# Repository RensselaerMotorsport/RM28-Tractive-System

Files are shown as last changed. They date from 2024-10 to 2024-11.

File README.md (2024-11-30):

# RM28-TRACTIVE-SYSTEM

This respository currently contains several projects for Rensselaer Motorsport's RM28 FSAE competition car, along with some documentation, and spreadsheets for BOMs and calcs
* WIP RM28 Project - This project is the most up-to-date version of the 2024-2025 competition car's High Voltage System.

To open and work with these files, use the following software:
* LTSpice - Circuit simulation software used for preliminary mockups of circuit designs. The .asc files can be opened in other spice programs like ngspice or pspice, but these circuits were originally drafted in LTSpice
* KiCad - PCB design software used for creating schematics for manufacturing. These are either stored in .kicad_pcb files, or are gerber files packed away in zip archives
* Excel - For viewing of BSPD trip curve calculation sheet

Typical Circuits:
* Brake System Plausability Device (BSPD) - The custom circuit for RM28's safety circuit, designed to connect to our shutdown circuit. This is a fully analog safety circuit that activate the shutdown circuit when unsafe conditions (competition rules) are met.
    * The sensor values used for this circuit include the current sensor through the motor, and the voltage sensor from the accelerator pedal
    * See BSPD Current Sensor Trip Calculator.xlsx inside ./BSPD/ for calculations to determine the threshold voltage to activate this section of the circuit
* Ready to Move Light (RTML)
   * Blinking red LED if voltage outside accumulator is >60V, and if GLV on 
   * Static green LED if voltage outside accumulator is <60V, and if GLV on
* Voltage Indicator - Turns on LED indicator if voltage outside the accumulator container is greater than 60V. Must work in absence of GLV.
* ESF - Shows overall design of racecar electrical system. Includes datasheets, circuit diagrams, electrical architecture, and part numbers.

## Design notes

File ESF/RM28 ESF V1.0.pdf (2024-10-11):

Status BLANK
BLANK
OK
1 | | OK
1 | | OK
750 Ohms

### 50 W

750 W
1170 | V | OK
| mF | BLANK
| | OK
| sec
| V
95 | % | OK
212.268 W

### 0.53 A 0.00 sec

#DIV/0! | J

#DIV/0! | W

| | BLANK
#N/A | V | #N/A

#N/A | A | #N/A

Discharge

Bus Capacitance

Voltage

power @15 sec

Precharge

# series

# parallel

Ohmite 850F750E

Resistance

Resistor

Relay

Precharge Res Energy to 90% Average Power

Peak current
time to 90%

Ratio

Cont power

time

End of precharge

Resistance
Cont power

Discharge time (to 60V)

Peak power
Peak current

power @15 sec

Additional Comments

ending ratio

Relay voltage rating
Peak power | Relay current rating

delta V

Relay current rating

Relay voltage rating

Rules References

Normal State

EV.5.6; EV.7.2.2c

#Public

BLANK
OK
1 | | OK
1 | | OK
750 | Ohms | | #N/A
50 | W | | #N/A
750 | W | OK | #N/A
1170 | V | OK
212.268 W

### 0.53 A

0 | s | OK
| | BLANK
#N/A | V | #N/A

#N/A | A | #N/A

#N/A | | #N/A

Discharge

Voltage

TSMP
Resistor

Resistance
Cont power

# parallel

# series

Resistor Ohmite 850F750E
# parallel

# series

Resistance
Cont power

Peak power
Peak current

power @15 sec
Voltage

Relay

Normal State

BLANK
BLANK
BLANK
BLANK
Ohms | #N/A
W | #N/A
V | #N/A

Rules References
EV.5.8.4

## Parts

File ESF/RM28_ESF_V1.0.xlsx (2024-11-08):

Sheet: Overview
Instructions |  |  | Status
Input Cells: Cells that require user input have an orange background. Status Indicators: Cells, sections, and worksheets each have an overall status, indicated by blue background cells. Images and Schematics: For sections requiring images or schematics, paste the image over the specified area. Use high-resolution images to allow for zooming if needed, and then resize the image appropriately. Datasheets: Provide a hyperlink to the manufacturer's datasheet where requested. Additional Comments: Sections labeled "Additional Comments" are provided for documenting anything the team feels is not adequately covered in the specified fields. Completing these sections is optional. |  |  | Datasheets | OK
 |  |  | TS Schematics | OK
 |  |  | Accumulator | WARNING
 |  |  | Precharge/Discharge | OK
 |  |  | Charging | OK
 |  |  | Shutdown Circuit | OK
 |  |  | Torque Security | OK
 |  |  | Other | OK
 |  |  | Team Name | Rensselaer Motorsport
 |  |  | University | Rensselaer Polytechnic Institute
 |  |  | Competition Year | 2025
 |  |  | Max TS Voltage | 399 | V
 |  |  | Accumulator Fuse | 200 | A
Additional Comments
Template Revision History
Version | Date | Comment
2.4 | 2024-09-30 | Updated for 2025 rules and terminology, general bug fixes.
2.3 | 2023-10-29 | Updated for 2024 season.
2.2 | 2022-11-03 | Updated for 2023 season.
2.1 | 2021-10-22 | Updated for 2022 season.
2.0 | 2020-11-27 | Multiple updates and bug fixes.

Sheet: Datasheets
Status | OK
Battery Cell |  |  |  | OK
Make |  | Molicel
Model |  | P28A
Nominal Capacity |  | 2.8 | Ahr
Maximum Voltage |  | 4.2 | V
Nominal Voltage |  | 3.6 | V
Minimum Voltage |  | 2.5 | V
Max output current |  | 35 | A
Max continuous current |  | 25 | A
Max Cell temp |  | 60 | C
Cell Chemistry |  | LiNiMnCoO2 (NMC)
Datasheet |  | https://www.molicel.com/wp-content/uploads/INR18650P28A-V1-80093.pdf
SDS |  | https://www.molicel.com/wp-content/uploads/00058ar-Molicel-SDS-Y2020.pdf
Additional Comments
Conductors |  |  |  |  |  |  |  |  | OK
Manufacturer | Part Number | Size [mm2] | Voltage [V] | Ampacity [A] | Max Temp [C] | Datasheet |  | Location Used |  | Additional Comments |  |  |  |  | Rules References
Exrad | EXRAD–EF/EF-KW-50 | 50 | 1000 | 275 | 140 | High current TS wire (https://www.champcable.com/wp-content/uploads/2020/08/220.-EXRAD-ERGOFLEX-ERGOFLEX-Shielded-Thick-Wall-Battery-Cable-R1.pdf) |  | Accumulator to motor (through energy meter and MSD on respective - and + lines) & interior of accumulator | OK |  |  |  |  |  | EV.5.2.1 EV.5.2.5 EV.6.3 EV.6.3.2 EV.6.6.4
AWC | M22759/22-22 (https://www.awcwire.com/product/m22759_22-22) | 0.34 | 600 | 0.92 | 200 | Low current TS wire (https://www.awcwire.com/product/m22759_22-22) |  | IMD, Precharge, Discharge | OK | HV to IMD and pre/discharge wiring
Team Manufactured | Series Bus Bars | 68.54825 | N/A | 200 | N/A | 1100-H14 aluminum (https://www.mcmaster.com/88685K95/) |  | Series Cell Connections, HV component connections | OK | See Series bus bar calculations to the right
Team Manufactured | Maintenance plug Vertical offset cylinder | 121.7350884 | N/A | 200 | N/A | 6061 Aluminum Rod (https://www.mcmaster.com/2655N21/) |  | Maintenance plug Vertical offset cylinder | OK
Team Manufactured | Component HV bus bars | 68.54825 | N/A | 200 | N/A | 1100-H14 aluminum (https://www.mcmaster.com/88685K95/) |  | HV between component connections | OK | See variable length bus bar calculations to the right, examples of use include between IRs and accumulator HV connector
Fuses |  |  |  |  |  |  |  |  | OK
Manufacturer | Part Number | Voltage [V] | AC/DC | Current [A] | Interrupt [A] | Datasheet |  | Location Used |  | Additional Comments |  |  |  |  | Rules References
Heraeus | AL-H11 | N/A | DC | 35 | 10000 | AL-H11 (https://datasheet.datasheetarchive.com/originals/crawler/heraeus.com/31fe58e96e1a05e1dcb559314f291a55.pdf) |  | Cell-level fuseable links on purchased modules | OK |  |  |  |  |  | EV.5.2.1 EV.6.6
Bel Fuse | 0ZCK0020FF2G (https://www.mouser.com/ProductDetail/Bel-Fuse/0ZCK0020FF2G?qs=SRYZG9HaIQ1YaXTwF3oUbw%3D%3D) | 24 | DC | 0.25 | 100 | Bel Fuse 0ZCK (https://www.belfuse.com/resources/datasheets/circuitprotection/ds-cp-0zck-series.pdf) |  | Voltage sense lines on purchased cell modules | OK
Bel Fuse | 0AKNBK200-BB (https://www.mouser.com/ProductDetail/Bel-Fuse/0AKNBK200-BB?qs=vvQtp7zwQdNf0nJ%2FatZ4hA%3D%3D) | 500 | DC | 200 | 50000 | Bel Fuse (https://www.belfuse.com/resources/datasheets/circuitprotection/ds-CP-0AKN-series.pdf) |  | Accumulator main fuse | OK
Schurter Inc. | 8020.5071.G (https://www.mouser.com/ProductDetail/Schurter/8020.5071.G?qs=YfC6cSmZ4rqo%252BdI%252BgQjFCw%3D%3D) | 400 | DC | 2 | 1500 | IMD Fuse (https://www.schurter.com/en/datasheet/typ_SHF_6.3x32.pdf) |  | IMD supply lines | OK | HV to IMD (needed due to wires >= 150mm)
Bel Fuse | 0ADKC5000-BE (https://www.mouser.com/ProductDetail/Bel-Fuse/0ADKC5000-BE?qs=HXFqYaX1Q2xXpuf%2FgyvHFg%3D%3D) | 500 | DC | 5 | 20000 | Energy Meter Fuse (https://www.mouser.com/datasheet/2/643/ds_cp_0adkx_series-1960352.pdf) |  | Energy meter positive line | OK
Resistors |  |  |  |  |  |  |  |  |  |  |  | OK
Manufacturer | Part Number | Voltage [V] | Resistance [Ω] | Power [W] | Power for 15 sec [W] | Heatsink [°C/W] (Enter "None" if no heatsink) |  |  | Datasheet |  | Location Used |  | Additional Comments & Heatsink Part Number(s) |  |  |  | Rules References
Ohmite | 850F750E (https://www.mouser.com/ProductDetail/Ohmite/850F750E?qs=%2Fkw1Ka6y2YmeEqAmz%252BCsrw%3D%3D) | 1170 | 750 | 50 | 750 | 3 |  |  | 850F750E (https://www.ohmite.com/assets/images/res-89.pdf) |  | Precharge/Discharge | OK | Manufacturer tests at 5x rated power for 5sec. 250W>212W peak. 50W>46W avg. |  |  |  | EV.5.2.1 EV.5.6 EV.5.8.4
Caddock Electronics Inc. | MP925-10.0K-1% (https://www.mouser.com/ProductDetail/Caddock/MP925-10.0K-1?qs=YqNA2qefETA%2FE%2Fk%2F%252BKWLww%3D%3D) | 500 | 10000 | 25 | N/A | None |  |  | MP925 (https://www.mouser.com/datasheet/2/62/MP9000_Series-1052.pdf) |  | TSMP | OK
Contactors/Relays |  |  |  |  |  |  |  |  | OK
Manufacturer | Part Number | Voltage [V] | Continuous Current [A] | Max Interrupt Current [A] | Normal State | Datasheet |  | Location Used |  | Additional Comments |  |  |  |  | Rules References
Kilovac | LEV200A4NAA (https://www.mouser.com/ProductDetail/TE-Connectivity-Kilovac/LEV200A4NAA?qs=FoJTTr54RLTOub1ORrXpDA%3D%3D) | 900 | 500 | 1.1 | NO | LEV200A4NAA (https://www.mouser.com/datasheet/2/418/9/ENG_CS_5_1773450_5_sec7_LEV200_0313_5_1773450_5_Se-3350705.pdf) |  | IRs, Inside Accumulator Container | OK |  |  |  |  |  | EV.5.2.1 EV.5.4 EV.5.6
Cynergy3 | DBT71205F-HR (https://www.mouser.com/ProductDetail/Cynergy3/DBT71205F-HR?qs=OlC7AqGiEDknK2jB3AhN5A%3D%3D) | 3500 | 3 | 2 | NC | DBT71205F-HR (https://www.mouser.com/datasheet/2/657/cynergy3_d_hr_v2-1892317.pdf) |  | Discharge | OK
Cynergy3 | DAT71205F-HR (https://www.mouser.com/ProductDetail/Cynergy3/DAT71205F-HR?qs=OlC7AqGiEDlIL4KVHc3FLw%3D%3D) | 3500 | 3 | 2 | NO | DAT71205F-HR (https://www.mouser.com/datasheet/2/657/cynergy3_d_hr_v2-1892317.pdf) |  | Precharge | OK
Connectors |  |  |  |  |  |  |  | OK
Manufacturer | Part Number | Voltage [V] | Ampacity [A] | Wire Size [mm2] | Datasheet |  | Location Used |  | Additional Comments |  |  |  |  | Rules References
Amphenol | MSDM5002 (https://www.mouser.com/ProductDetail/Amphenol-PCD-Shenzhen/MSDM5002?qs=LcEtihlZWqbc1RsOqxB6zA%3D%3D) | 1000 | 500 | 50 | MSD Plug (https://www.mouser.com/datasheet/2/18/1/msd_m_xxxx_rev_a_cdr-1853453.pdf) |  | MSD Plug | OK |  |  |  |  |  | EV.5.2.1 EV.5.9 EV.6.3.3
Amphenol | MSDF000R (https://www.mouser.com/ProductDetail/Amphenol-PCD-Shenzhen/MSDF000R?qs=LcEtihlZWqaGMLWux0l6Dw%3D%3D) | 1000 | 500 | 50 | MSD Receptacle (https://www.mouser.com/datasheet/2/18/Amphenol_08092019_MSDF000R-1626989.pdf) |  | MSD Receptacle | OK
Amphenol | PL082Y-301-10M6-2 (https://www.mouser.com/ProductDetail/Amphenol-Technical-Products/PL082Y-301-10M6-2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) | 1000 | 300 | 50 | PL082Y-301-10M6-2 (https://www.mouser.com/datasheet/2/18/1/Amphneol_01182021_PowerLok_G2_Product_Catalog_2020-1955456.pdf) |  | HV Out Receptacle | OK
Amphenol | PL282Y-301-50 (https://www.mouser.com/ProductDetail/Amphenol-Technical-Products/PL282Y-301-50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) | 1000 | 300 | 50 | PL282Y-301-50 (https://www.mouser.com/datasheet/2/18/1/c_powerlok_right_angle_plugs_1_2_3_way_cdr-1701769.pdf) |  | HV Out Plug | OK
Team Manufactured | Maintenance Plug Bus Bar | N/A | 200 | 68.54825 | 1100-H14 aluminum (https://www.mcmaster.com/88685K95/) |  | Maintenance Plugs | OK | See calculations to the right
Littelfuse | 03450613H | 600 | 20 | N/A | Energy meter fuse holder (https://www.molex.com/en-us/products/part-detail/192210241?display=pdf) |  | Energy meter fuse holder | OK | Soldered terminals, low current fuse
Amphenol | HVSL633063A106I | 800 | 40 | 16 | AC In (https://mgchemicals.com/downloads/tds/tds-4223f-l.pdf) |  | Charger input | OK | AC in to charger
Pomona Electronics | 72930 | 1000 | 36 | N/A | TSMP (https://www.awcwire.com/product/m22759_22-22) |  | TSMP - start panel | OK | TSMP connector. One red, one black, same part electrically
Molex | 192210241 | N/A | 230 | 55 | TS Ring Terminals (https://www.mouser.com/ProductDetail/Bel-Fuse/0ADKC5000-BE?qs=HXFqYaX1Q2xXpuf%2FgyvHFg%3D%3D) |  | Energy meter, Motor, MSD, Main fuse, IRs | OK | Ring terminals crimped onto main TS cable. Used in various locations when attaching to bolted connection (HVD, energy meter, motor phases, main fuse, AIRs)
Insulating Materials |  |  |  |  |  |  |  |  |  | OK
Manufacturer | Part Number | Thickness [mm] | Dielectric strength [V/mm] | Voltage Rating [V] | Max Temp [C] | Flammability Rating | Datasheet |  | Location Used |  | Additional Comments |  |  |  |  | Rules References
McMaster-Carr | 85345K651 | 62.5 | 350 | 21875 | 137.778 | UL 94 V-0 | Accumulator plate hard insulation (https://www.mcmaster.com/85345K651/) |  | Accumulator | OK | Used on the underside of the horizontal plate that divides segments from components |  |  |  |  | EV.5.2.1 EV.5.2.2.a EV.5.2.3 EV.5.4.4 EV.6.2 EV.6.5.5.a
MYJOR | Kapton Tape | 1 | 4500 | 4500 | 350 | N/A | Kapton tape (https://www.amazon.com/Temperature-Kapton-Professional-Protecting-Circuit/dp/B08NY4914D) |  | Segments, accumulator container edges, motor connections | OK
CIE Solutions | Gen 2 Lithium Block Module | 3.4 | 26000 | 88400 | 105 | UL 94 V-0 | Cell modules (https://www.cie-solutions.com/lithium-block-gen2) |  | Modules | OK | Purchased modules made of Glass-Filled Fire Retardent ABS
3M | FP-301 | 0.76 | 789.4736842 | 600 | 125 | N/A | Bus bar heat shrink (https://multimedia.3m.com/mws/media/23031O/3m-heat-shrink-tubing-fp-301-data-sheet.pdf) |  | Bus Bars | OK
3DX Tech | PCA03FR200750BK00 | 5 | 26000 | 130000 | 137 | UL 94 V-0 | 3D printing filament (https://cdn.shopify.com/s/files/1/0625/4185/6821/files/FIREWIRE_FR_PCABS_TDS_v3.pdf?v=1723942765) |  | Maintainence Plug Handle | OK
Dupont | 93554 | 0.13 | 28150 | 3659.5 | 220 | UL 94 V-0 | Nomex (https://materials-direct.com/product/dupont-nomex-410-0-13mm/) |  | Segement dividing walls, accumulator container inside walls | OK
MG Chemicals | 4223F-55ML | 2 | 1000 | 2000 | 125 | N/A | Conformal Coat (https://mgchemicals.com/downloads/tds/tds-4223f-l.pdf) |  | Team manufactured PCBs (RTM, Voltage Indicator, etc.) | OK | UV-A flourescent
Anti Seize Technology | 17214 | 0.0508 | 66929 | 3399.9932 | 121 | N/A | Insulative Spray Coating (https://www.grainger.com/product/ANTI-SEIZE-TECHNOLOGY-Insulating-Varnish-Red-34D505) |  | Container walls, segment mounting brackets | OK

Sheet: TS Schematics
Status | OK
Tractive System Schematic |  |  |  |  | Accumulator TS Schematic |  |  |  | Additional Comments
 |  |  |  |  |  |  |  |  | Voltage Indicator Schematic:
Vehicle Tractive System Schematic Shows |  |  |  | OK | Accumulator TS Schematic Shows |  |  | OK
Rules References |  |  |  |  | Rules References
 |  | Shows details of all TS circuits outside of accumulator | TRUE | OK |  | Details of all TS circuits within accumulator | TRUE | OK
 |  | Accumulator is shown as a single element (without internal details) | TRUE | OK |  | All wire gauges labeled | TRUE | OK
 |  | All wire gauges labeled | TRUE | OK |  | All fuses labeled with ampacity | TRUE | OK
 |  | All fuses labeled with ampacity | TRUE | OK | EV.6.6.6 | All wires > 150mm have a fuse within the first 150mm from the source | TRUE | OK
EV.6.6.6 |  | All wires > 150mm have a fuse within the first 150mm from the source | TRUE | OK |  | Fuse locations represent physical location | TRUE | OK
 |  | Fuse locations represent physical location | TRUE | OK |  | Connectors labeled with Make/Model | TRUE | OK
 |  | Enclosures shown | TRUE | OK |  | Standard schematic symbols used | TRUE | OK
 |  | Connectors labeled with Make/Model | TRUE | OK |  | All text is readable (zooming is allowed) | TRUE | OK
 |  | Standard schematic symbols used | TRUE | OK | EV.5.4 | IRs | TRUE | OK
 |  | All text is readable (zooming is allowed) | TRUE | OK | EV.5.3 | Maintenance plugs | TRUE | OK
EV.5.8 |  | TSMPs | TRUE | OK |  | Cells (details of all intercell connections may be abstracted) | TRUE | OK
 |  | Motor Controller | TRUE | OK | EV.5.7 | Accumulator Indicator (must be powered directly by TS) | TRUE | OK
 |  | Motor | TRUE | OK
EV.5.8.5 |  | TSMPs not fused | TRUE | OK
Must be shown on at least one schematic |  |  |  | OK
Rules References
EV.7.6 |  | IMD | TRUE | OK
EV.5.5 |  | MSD | TRUE | OK
EV.5.6 |  | Precharge | TRUE | OK
EV.5.6 |  | Discharge | TRUE | OK
EV.3.2; EV.5.1.3 |  | Energy Meter (shunt and TS sense connection) | TRUE | OK
EV.5.6.3.b |  | Discharge still functions when MSD is opened | TRUE | OK
EV.5.6.3.c |  | Discharge is not fused | TRUE | OK

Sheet: Accumulator
Status | WARNING
Segment-to-Segment Connection |  |  |  | Series |  | OK
Maximum TS Voltage |  |  |  | 399 | V | OK
Nominal TS Voltage |  |  |  | 342 | V
Total Cells |  |  |  | 570
Segment Data |  |  |  |  |  |  |  |  | OK | BMS |  |  |  |  | WARNING | Maintenance Plugs |  |  |  | OK | Insulating Materials |  |  |  |  | OK | Additional Comments
Cell Connection Order |  |  | Parallel then Series |  |  |  |  |  | OK | BMS Type |  |  | Centralized |  | OK | Connector |  | Team Manufactured Maintenance Plug Bus Bar |  | OK | Between cells and accum. container |  |  | Dupont 93554 |  | OK
Segment | Parallel cells | Series cells | Temp Sensors | Accumulator Number | Max Voltage [V] |  | Segment Energy [MJ] |  |  | BMS Source |  |  | Purchased |  | OK | Ampacity |  | 200 | A | OK | Voltage Rating |  |  | 3659.5 | V | OK
 |  |  |  |  |  |  |  |  |  | Make | Orion | Model | BMS2 180-Cell |  | OK | Segment Fuse |  |  |  |  | Temperature Rating |  |  | 220 | C | OK
1 | 6 | 19 | 95 | 1 | 79.8 |  | 4.826304 |  | OK | Galvanic Isolation TS to GLV |  |  | 1500 | V | OK | Segment Fuse Ampacity |  | #N/A | A |  | Flammability Rating |  |  | UL 94 V-0
2 | 6 | 19 | 95 | 1 | 79.8 |  | 4.826304 |  | OK | Galvanic Isolation between segments |  |  | 2500 | V | OK | IR |  |  |  |  | On top of cells |  |  | CIE Solutions Gen 2 Lithium Block Module |  | OK
3 | 6 | 19 | 95 | 1 | 79.8 |  | 4.826304 |  | OK | Galvanic Isolation device |  |  |  |  |  | Make/Model |  | Kilovac LEV200A4NAA |  | OK | Voltage Rating |  |  | 88400 | V | OK
4 | 6 | 19 | 95 | 1 | 79.8 |  | 4.826304 |  | OK | Gavlanic Isolation device datasheet |  |  |  |  |  | Contact Voltage Rating |  | 900 | V | OK | Temperature Rating |  |  | 105 | C | OK
5 | 6 | 19 | 95 | 1 | 79.8 |  | 4.826304 |  | OK | Voltage Sense Leads |  |  |  |  |  | Max switching current |  | 1.1 | A |  | Flammability Rating |  |  | UL 94 V-0
6 |  |  |  |  | 0 |  | 0 |  |  | Maximum Unfused Lead Length |  |  | 5 | mm | OK | Max continuous current |  | 500 | A | OK | Separating IRs and Fuse from cells |  |  | McMaster-Carr 85345K651 |  | OK
7 |  |  |  |  | 0 |  | 0 |  |  | Sense Lead Overcurrent Protection Device |  |  | Bel Fuse 0ZCK0020FF2G |  | OK | Main Fuse |  |  |  |  | Voltage Rating |  |  | 21875 | V | OK
8 |  |  |  |  | 0 |  | 0 |  |  | Overcurrent Location |  |  | BMS PCB |  | OK | Main Fuse |  | Bel Fuse 0AKNBK200-BB |  | OK | Temperature Rating |  |  | 137.778 | C | OK
9 |  |  |  |  | 0 |  | 0 |  |  | Overcurrent Other Location |  |  |  |  |  | Main fuse ampacity |  | 200 | A |  | Flammability Rating |  |  | UL 94 V-0
10 |  |  |  |  | 0 |  | 0 |  |  | Overcurrent Voltage Rating |  |  | 24 | V | WARNING | Main fuse voltage |  | 500 | V | OK
11 |  |  |  |  | 0 |  | 0 |  |  | Temperature Sensors |  |  |  |  |  | MSD
12 |  |  |  |  | 0 |  | 0 |  |  | Temp Sensor Location |  |  | On cell terminal |  | OK | MSD |  | Amphenol MSDM5002 |  | OK
13 |  |  |  |  | 0 |  | 0 |  |  | Distance to cell terminal |  |  |  | mm |  | Ampacity |  | 500 | A | OK
14 |  |  |  |  | 0 |  | 0 |  |  | Cells sensed per sensor |  |  | 1 | cells | OK
15 |  |  |  |  | 0 |  | 0 |  |  | Thermal Contact material used |  |  | 3M Scotch-Weld Epoxy Adhesive 2216
16 |  |  |  |  | 0 |  | 0 |  |  | Thermal contact material datasheet |  |  | https://multimedia.3m.com/mws/media/2366022O/3m-scotch-weld-epoxy-adhesive-2216-b-a-gray.pdf |  | OK
17 |  |  |  |  | 0 |  | 0 |  |  | Thermal contact material conductivity |  |  | 0.394 | W/(m∙K) | OK
18 |  |  |  |  | 0 |  | 0 |  |  | Thermal contact material thickness |  |  | 1 | mm | OK
 |  |  |  |  |  |  |  |  |  | Percent of cells sensed |  |  | 83.33333333 | % | OK
Picture of Maintenance Plugs |  |  |  |  |  |  |  |  | Picture of Cell Connections |  |  |  |  |  |  |  | Picture of Temperature Sensor Location |  |  |  |  |  |  | Picture of Fuse and IRs Separation from Cells |  |  |  |  |  | Picture of Segment Insulation between Cell Terminals and Sides of Accumulator Container |  |  | Picture of Insulation on Top of Segment
Maintenance Plug(s) Picture Shows |  |  |  |  |  |  | OK |  | Cell Connections Picture Shows |  |  |  |  |  | OK |  | Temperature Sensor Picture Shows |  |  |  |  |  | OK | Fuse and IRs Separation Picture Shows |  |  |  |  | OK | Segment Insulation Picture Shows |  | OK | Segment Insulation Picture Shows |  | OK
Unique Configuration of plugs |  |  |  |  |  | TRUE | OK |  | Bolted connections have positive locking |  |  |  |  | TRUE | OK |  | Temp sensor in direct contact with terminal or busbar |  |  |  |  | TRUE | OK | Fuse and IRs are separated from cells |  |  |  | TRUE | OK | Insulation between cells and accumulator container | TRUE | OK | Insulation on top of cells (air not acceptable) | TRUE | OK
Non-conductive on un-necessary surface |  |  |  |  |  | TRUE | OK |  | Location of parallel cell overcurrent for parallel cells |  |  |  |  | TRUE | OK |  | Distance from sensor to cell negative terminal connection |  |  |  |  | TRUE | OK | Additional Comments |  |  |  |  | Rules References | Additional Comments |  | Rules References | Additional Comments |  | Rules References
Accessible without any additional accumulator disassembly |  |  |  |  |  | TRUE | OK |  | BMS voltage sense fuse location |  |  |  |  | TRUE | OK |  | Additional Comments |  |  |  |  |  | Rules References | The fuse is the flat dark green box on the top left. The fuse and IRs are separated by a 4130 steel plate as well as Nomex paper which are both nonflamable. The insulation is where the two highlighted blue lines are in the image |  |  |  |  | EV.5.4.4 | Insulation is nomex paper which will be placed on walls, pictured in blue and teal. As well there will be insulation on the interior walls on the sides and back pictured in pink. Highlighted in light blue is where G10 insulation will be placed on the top of the segement enclosure |  | EV.5.2.2.a EV.5.2.3 | Insulation is Fire Retardant, Glass Filled ABS |  | EV.5.2.2.a EV.5.2.3
Positive Locking |  |  |  |  |  | TRUE | OK |  | Additional Comments |  |  |  |  |  | Rules References |  | Thermistor directly on negative cell terminal. No dimension needed |  |  |  |  |  | EV.7.5
Additional Comments |  |  |  |  |  |  | Rules References |  | Nylon patch bolts into OEM component, left is series connections, right is parallel (fused, wire bonded) connections |  |  |  |  |  | EV.6.4.1 EV.6.4.3 EV.7.4.4.a
Our maintainence plug solution uses a nylon patch bolt to hold down an elevated bus bar connected to the end module of the segment. The bolts have a 3d printed cap(in yellow) made of FR ABS that are bonded to the bolts to unscrew without tools. The elevated aluminum cylinder will have a cover over it similar to the bus bar covers to ensure it can not be accidentally touched. Bus bars will be removed using an ABS printed attachment. |  |  |  |  |  |  | EV.5.3
Parallel Cell Fusing |  |  |  |  | WARNING | Rules Referenes
Source |  |  | Purchased |  | OK | EV.6.6.3 EV.6.6.5
Make/Model |  |  | Heraeus AL-H11 |  | OK
Continuous Current |  |  | 35 | A | WARNING
Continuous Current |  |  |  | A
Test Data Summary
Tests at current 1 |  |  | 0 |  |  |  |  | #N/A
Tests at current 2 |  |  | 0 |  |  |  | #N/A | #N/A
Tests at current 3 |  |  | 0 |  |  |  | #N/A
Tests at current 4 |  |  | 0
See Fusible Link Testing Guideline on FSAEOnline.com
Testing | Current [A] | Time to blow [s]
Test 1
Test 2
Test 3
Test 4
Test 5
Test 6
Test 7
Test 8
Test 9
Test 10
Test 11
Test 12
Test 13
Test 14
Test 15
Test 16

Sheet: PrechargeDischarge
Status | OK
Precharge |  |  |  | OK | Discharge |  |  | OK | Vehicle TSMP |  |  | OK | Rules References
Resistor |  | Ohmite 850F750E |  | OK | Resistor | Ohmite 850F750E |  | OK | Resistor | Caddock Electronics Inc. MP925-10.0K-1% |  | OK | EV.5.8.4
# parallel |  | 1 |  | OK | # parallel | 1 |  | OK | # parallel | 1 |  | OK
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

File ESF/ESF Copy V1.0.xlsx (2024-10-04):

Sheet: Overview
Instructions |  |  | Status
-All cells for input have an orange background. -Cells, sections and worksheets have an overall status. The status cells have a blue background. -For sections which require an image or schematic, the image should be pasted and located over the specified area. Images should be pasted at a high resolution and then resized. This allows the reader to zoom into the image if more resolution is required. -Where datasheets are requested, a hyperlink to the datasheet from the manufacturer must be provided. -Additional Comments sections are provided throughout for documentation of things which the team feels are not adequately documented in the provided fields. These are optional and do not need to be completed. |  |  | Datasheets | BLANK
 |  |  | TS Schematics | BLANK
 |  |  | Accumulator | BLANK
 |  |  | Precharge/Discharge | BLANK
 |  |  | Charging | BLANK
 |  |  | Shutdown Circuit | BLANK
 |  |  | Torque Security | BLANK
 |  |  | Other | BLANK
 |  |  | Team Name | Rensselaer Motorsport
 |  |  | University | Rensselaer Polytechnic Insitute
 |  |  | Competition Year | 2024
 |  |  | Max TS Voltage | 399 | V
 |  |  | Accumulator Fuse | #N/A | A
Additional Comments
Template Revision History
Version | Date | Comment
2.3 | 2023-10-29 | Updated for 2024 season.
2.2 | 2022-11-03 | Updated for 2023 season.
2.1 | 2021-10-22 | Updated for 2022 season.
2.0 | 2020-11-27 | Multiple updates and bug fixes.

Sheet: Datasheets
Status | BLANK
Battery Cell |  |  |  | OK
Make |  | Molicel
Model |  | P28A
Nominal Capacity |  | 2.8 | Ahr
Maximum Voltage |  | 4.2 | V
Nominal Voltage |  | 3.6 | V
Minimum Voltage |  | 2.5 | V
Max output current |  | 35 | A
Max continuous current |  | 25 | A
Max Cell temp |  | 60 | C
Cell Chemistry |  | LiNiMnCoO2 (NMC)
Datasheet |  | https://www.molicel.com/wp-content/uploads/INR18650P28A-V1-80093.pdf
SDS |  | https://www.molicel.com/wp-content/uploads/00058ar-Molicel-SDS-Y2020.pdf
Additional Comments
Conductors |  |  |  |  |  |  |  |  | BLANK
Manufacturer | Part Number | Size [mm2] | Voltage [V] | Ampacity [A] | Max Temp [C] | Datasheet |  | Location Used |  | Additional Comments |  |  |  |  | Rules References
 |  |  |  |  |  |  |  |  | BLANK |  |  |  |  |  | EV.5.2.1 EV.5.2.5 EV.6.3 EV.6.3.2 EV.6.6.4
Fuses |  |  |  |  |  |  |  |  | BLANK
Manufacturer | Part Number | Voltage [V] | AC/DC | Current [A] | Interrupt [A] | Datasheet |  | Location Used |  | Additional Comments |  |  |  |  | Rules References
 |  |  |  |  |  |  |  |  | BLANK |  |  |  |  |  | EV.5.2.1 EV.6.6
Resistors |  |  |  |  |  |  |  |  |  |  |  | BLANK
Manufacturer | Part Number | Voltage [V] | Resistance [Ω] | Power [W] | Power for 15 sec [W] | Heatsink [°C/W] (Enter "None" if no heatsink) |  |  | Datasheet |  | Location Used |  | Additional Comments |  |  |  | Rules References
 |  |  |  |  |  |  |  |  |  |  |  | BLANK |  |  |  |  | EV.5.2.1 EV.5.6 EV.5.8.4
Contactors/Relays |  |  |  |  |  |  |  |  | BLANK
Manufacturer | Part Number | Voltage [V] | Continuous Current [A] | Max Interrupt Current [A] | Normal State | Datasheet |  | Location Used |  | Additional Comments |  |  |  |  | Rules References
 |  |  |  |  |  |  |  |  | BLANK |  |  |  |  |  | EV.5.2.1 EV.5.4 EV.5.6
Connectors |  |  |  |  |  |  |  | BLANK
Manufacturer | Part Number | Voltage [V] | Ampacity [A] | Wire Size [mm2] | Datasheet |  | Location Used |  | Additional Comments |  |  |  |  | Rules References
 |  |  |  |  |  |  |  | BLANK |  |  |  |  |  | EV.5.2.1 EV.5.10 EV.6.3.3
Insulating Materials |  |  |  |  |  |  |  |  |  | BLANK
Manufacturer | Part Number | Thickness [mm] | Dielectric strength [V/mm] | Voltage Rating [V] | Max Temp [C] | Flammability Rating | Datasheet |  | Location Used |  | Additional Comments |  |  |  |  | Rules References
 |  |  |  |  |  |  |  |  |  | BLANK |  |  |  |  |  | EV.5.2.1 EV.5.2.2.a EV.5.2.3 EV.5.4.4 EV.6.2 EV.6.5.5.a

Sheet: TS Schematics
Status | BLANK
Tractive System Schematic |  |  |  | Accumulator TS Schematic |  |  | Additional Comments
Vehicle Tractive System Schematic Shows |  |  | BLANK | Accumulator TS Schematic Shows |  | BLANK
Rules References |  |  |  | Rules References
 |  | Shows details of all TS circuits outside of accumulator | BLANK |  | Details of all TS circuits within accumulator | BLANK
 |  | Accumulator is shown as a single element (without internal details) | BLANK |  | All wire gauges labeled | BLANK
 |  | All wire gauges labeled | BLANK |  | All fuses labeled with ampacity | BLANK
 |  | All fuses labeled with ampacity | BLANK | EV.6.6.6 | All wires > 150mm have a fuse within the first 150mm from the source | BLANK
EV.6.6.6 |  | All wires > 150mm have a fuse within the first 150mm from the source | BLANK |  | Fuse locations represent physical location | BLANK
 |  | Fuse locations represent physical location | BLANK |  | Connectors labeled with Make/Model | BLANK
 |  | Enclosures shown | BLANK |  | Standard schematic symbols used | BLANK
 |  | Connectors labeled with Make/Model | BLANK |  | All text is readable (zooming is allowed) | BLANK
 |  | Standard schematic symbols used | BLANK | EV.5.4 | AIRs | BLANK
 |  | All text is readable (zooming is allowed) | BLANK | EV.5.3 | Maintenance plugs | BLANK
EV.5.8 |  | TSMPs | BLANK |  | Cells (details of all intercell connections may be abstracted) | BLANK
 |  | Motor Controller | BLANK | EV.5.7 | Accumulator Indicator | BLANK
 |  | Motor | BLANK
EV.5.8.5 |  | TSMPs not fused | BLANK
Must be shown on at least one schematic |  |  | BLANK
Rules References
EV.7.6 |  | IMD | BLANK
EV.5.5 |  | HVD | BLANK
EV.5.6 |  | Precharge | BLANK
EV.5.6 |  | Discharge | BLANK
EV.3.2; EV.5.1.3 |  | Energy Meter | BLANK
EV.5.6.1.c |  | Precharge is not fused | BLANK
EV.5.6.1.c |  | Discharge is not fused | BLANK

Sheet: Accumulator
Status | BLANK
Segment-to-Segment Connection |  |  |  | Series |  | OK
Maximum TS Voltage |  |  |  | 399 | V | OK
Nominal TS Voltage |  |  |  | 342 | V
Total Cells |  |  |  | 570
Segment Data |  |  |  |  |  |  |  |  | OK | BMS |  |  |  |  | BLANK | Maintenance Plugs |  |  |  | BLANK | Insulating Materials |  |  |  | BLANK | Additional Comments
Cell Connection Order |  |  | Parallel then Series |  |  |  |  |  | OK | BMS Type |  |  | Centralized |  | OK | Connector |  |  |  | BLANK | Between cells and accum. container |  |  |  | BLANK
Segment | Parallel cells | Series cells | Temp Sensors | Accumulator Number | Max Voltage [V] |  | Segment Energy [MJ] |  |  | BMS Source |  |  | Purchased |  | OK | Ampacity |  | #N/A | A | BLANK | Voltage Rating |  | #N/A | V | BLANK
 |  |  |  |  |  |  |  |  |  | Make | Orion | Model | BMS2 180-Cell |  | OK | Segment Fuse |  |  |  |  | Temperature Rating |  | #N/A | C | BLANK
1 | 6 | 19 | 95 | 1 | 79.8 |  | 4.826304 |  | OK | Galvanic Isolation TS to GLV |  |  | 1500 | V | OK | Segment Fuse Ampacity |  | #N/A | A |  | Flammability Rating |  | #N/A
2 | 6 | 19 | 95 | 1 | 79.8 |  | 4.826304 |  | OK | Galvanic Isolation between segments |  |  | 2500 | V | OK | AIR |  |  |  |  | On top of cells |  |  |  | BLANK
3 | 6 | 19 | 95 | 1 | 79.8 |  | 4.826304 |  | OK | Galvanic Isolation device |  |  |  |  |  | Make/Model |  |  |  | BLANK | Voltage Rating |  | #N/A | V | BLANK
4 | 6 | 19 | 95 | 1 | 79.8 |  | 4.826304 |  | OK | Gavlanic Isolation device datasheet |  |  |  |  |  | Contact Voltage Rating |  | #N/A | V | BLANK | Temperature Rating |  | #N/A | C | BLANK
5 | 6 | 19 | 95 | 1 | 79.8 |  | 4.826304 |  | OK | Voltage Sense Leads |  |  |  |  |  | Max switching current |  | #N/A | A |  | Flammability Rating |  | #N/A
6 |  |  |  |  | 0 |  | 0 |  |  | Max Sense Lead Length |  |  |  | cm | BLANK | Max continuous current |  | #N/A | A | BLANK | Separating AIR and Fuse from cells |  |  |  | BLANK
7 |  |  |  |  | 0 |  | 0 |  |  | Sense Lead Overcurrent Protection Device |  |  |  |  | BLANK | Main Fuse |  |  |  |  | Voltage Rating |  | #N/A | V | BLANK
8 |  |  |  |  | 0 |  | 0 |  |  | Overcurrent Location |  |  |  |  | BLANK | Main Fuse |  |  |  | BLANK | Temperature Rating |  | #N/A | C | BLANK
9 |  |  |  |  | 0 |  | 0 |  |  | Overcurrent Other Location |  |  |  |  |  | Main fuse ampacity |  | #N/A | A |  | Flammability Rating |  | #N/A
10 |  |  |  |  | 0 |  | 0 |  |  | Overcurrent Voltage Rating |  |  | #N/A |  | BLANK | Main fuse voltage |  | #N/A | V | #N/A
11 |  |  |  |  | 0 |  | 0 |  |  | Temperature Sensors
12 |  |  |  |  | 0 |  | 0 |  |  | Temp Sensor Location |  |  | On cell terminal |  | OK
13 |  |  |  |  | 0 |  | 0 |  |  | Distance to cell terminal |  |  |  | mm
14 |  |  |  |  | 0 |  | 0 |  |  | Cells sensed per sensor |  |  | 1 | cells | OK
15 |  |  |  |  | 0 |  | 0 |  |  | Thermal Contact material used
16 |  |  |  |  | 0 |  | 0 |  |  | Thermal contact material datasheet
17 |  |  |  |  | 0 |  | 0 |  |  | Thermal contact material conductivity |  |  |  | W/(m∙K)
18 |  |  |  |  | 0 |  | 0 |  |  | Thermal contact material thickness |  |  |  | mm
 |  |  |  |  |  |  |  |  |  | Percent of cells sensed |  |  | 83.33333333 | % | OK
Picture of Maintenance Plugs |  |  |  |  |  |  |  |  | Picture of Cell Connections |  |  |  |  |  |  |  | Picture of Temperature Sensor Location |  |  |  |  |  | Picture of Fuse and AIR Separation from Cells |  |  |  |  | Picture of Segment Insulation between Cell Terminals and Sides of Accumulator Container |  | Picture of Insulation on Top of Segment
Maintenance Plug(s) Picture Shows |  |  |  |  |  |  | BLANK |  | Cell Connections Picture Shows |  |  |  |  |  | BLANK |  | Temperature Sensor Picture Shows |  |  |  |  | BLANK | Fuse and AIR Separation Picture Shows |  |  |  | BLANK | Segment Insulation Picture Shows | BLANK | Segment Insulation Picture Shows | BLANK
Unique Configuration of plugs |  |  |  |  |  |  | BLANK |  | Bolted connection have positive locking |  |  |  |  |  | BLANK |  | Temp sensor in direct contact with terminal or busbar |  |  |  |  | BLANK | Fuse and AIR are separated from cells |  |  |  | BLANK | Insulation between cells and accumulator container | BLANK | Insulation on top of cells (air not acceptable) | BLANK
Non-conductive on un-necessary surface |  |  |  |  |  |  | BLANK |  | location of parallel cell overcurrent for parallel cells |  |  |  |  |  | BLANK |  | Distance from sensor to cell negative terminal |  |  |  |  | BLANK | Additional Comments |  |  |  | Rules References | Additional Comments | Rules References | Additional Comments | Rules References
Accessible without any additional accumulator disassembly |  |  |  |  |  |  | BLANK |  | Additional Comments |  |  |  |  |  | Rules References |  | Additional Comments |  |  |  |  | Rules References |  |  |  |  | EV.5.4.4 |  | EV.5.2.2.a EV.5.2.3 |  | EV.5.2.2.a EV.5.2.3
Positive Locking |  |  |  |  |  |  | BLANK |  |  |  |  |  |  |  | EV.6.4.1 EV.6.4.3 |  |  |  |  |  |  | EV.7.5
Additional Comments |  |  |  |  |  |  | Rules References
 |  |  |  |  |  |  | EV.5.3
Parallel Cell Fusing |  |  |  |  | BLANK | Rules Referenes
Source |  |  | Purchased |  | OK | EV.6.6.3 EV.6.6.5
Make/Model |  |  |  |  | BLANK
Continuous Current |  |  | #N/A | A | BLANK
Continuous Current |  |  |  | A
Test Data Summary
Tests at current 1 |  |  | 0 |  |  |  |  | 0
Tests at current 2 |  |  | 0 |  |  |  | #NUM! | 0
Tests at current 3 |  |  | 0 |  |  |  | #NUM!
Tests at current 4 |  |  | 0
See Fusible Link Testing Guideline on FSAEOnline.com
Testing | Current [A] | Time to blow [s]
Test 1
Test 2
Test 3
Test 4
Test 5
Test 6
Test 7
Test 8
Test 9
Test 10
Test 11
Test 12
Test 13
Test 14
Test 15
Test 16

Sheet: PrechargeDischarge
Status | BLANK
Precharge |  |  |  | BLANK | Discharge |  |  | BLANK | TSMP |  |  | BLANK | Rules References
Resistor |  |  |  | BLANK | Resistor |  |  | BLANK | Resistor |  |  | BLANK | EV.5.8.4
# parallel |  |  |  | BLANK | # parallel |  |  | BLANK | # parallel |  |  | BLANK
# series |  |  |  | BLANK | # series |  |  | BLANK | # series |  |  | BLANK
Resistance |  | #N/A | Ohms |  | Resistance | #N/A | Ohms |  | Resistance | #N/A | Ohms | #N/A
Cont power |  | #N/A | W |  | Cont power | #N/A | W |  | Cont power | #N/A | W | #N/A
power @15 sec |  | #N/A | W |  | power @15 sec | #N/A | W | #N/A | Voltage | #N/A | V | #N/A
Voltage |  | #N/A | V | #N/A | Voltage | #N/A | V | #N/A
Bus Capacitance |  |  | mF | BLANK | Peak power | #N/A | W
End of precharge |  |  |  | BLANK | Peak current | #N/A | A
time |  |  | sec |  | Discharge time (to 60V) | #N/A | s | #N/A
delta V |  |  | V |  | Relay |  |  | BLANK
ending ratio |  |  | % |  | Relay voltage rating | #N/A | V | #N/A
Peak power |  | #N/A | W |  | Relay current rating | #N/A | A | #N/A
Peak current |  | #N/A | A |  | Normal State | #N/A |  | #N/A
time to 90% |  | #N/A | sec |  | Rules References
Precharge Res Energy to 90% |  | #N/A | J |  | EV.5.6; EV.7.2.2c
Average Power |  | #N/A | W
Relay |  |  |  | BLANK
Relay voltage rating |  | #N/A | V | #N/A
Relay current rating |  | #N/A | A | #N/A
Additional Comments

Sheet: Charging
Status | BLANK
Charger |  |  |  |  | OK | Additional Comments
Make |  |  | Elcon |  | OK
Model |  |  | 6.6kW HK-J CAN UHF |  | OK
Datasheet |  |  | Elcon Charger (https://www.electricmotorsport.com/ev-parts/chargers/multi-chemistry/elcon-6-6kw-hk-j-can-uhf-charger.html) |  | OK
Input Voltage |  |  | 85~265 | V | OK
Input Current |  |  | 32A | A | OK
Output Voltage |  |  | 170-650 | V | OK
Output Current |  |  | 12 | A | OK
Power |  |  | 6.6 | kW | OK
Input to Output isolation |  |  | 2000 VAC 10 mA |  | OK
Charging Tractive System Schematic |  |  |  |  |  |  | Charging Shutdown Circuit
Charging Tractive System Schematic Shows |  |  |  |  |  | BLANK | Charging Shtdown Circuit Shows |  | BLANK
Rules References |  |  |  |  |  |  | Rules References
 |  | Fuse |  |  |  | BLANK | EV.8.3 | IMD Control and Powerstage | BLANK
 |  | Connectors |  |  |  | BLANK | EV.8.3 | AMS | BLANK
 |  | Wire Gauge |  |  |  | BLANK | EV.8.2.7 | Charger Shutdown Button | BLANK
EV.8.4 |  | IMD |  |  |  | BLANK | EV.8.4 | AIRs | BLANK
EV.8.4.2 |  | AIRs |  |  |  | BLANK |  | Charge Connector Interlock | BLANK
EV.8.2.6 |  | TSMPs |  |  |  | BLANK |  | Charge Control (CAN, Enable, etc.) | BLANK
Additional Comments |  |  |  |  |  |  | Additional Comments

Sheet: Shutdown Circuit
Status | BLANK
IMD |  |  |  |  | OK | BSPD |  |  |  | BLANK
Rules Reference |  |  | EV.7.6 |  |  | Rules Reference |  | EV.7.7
Make/Model |  |  | Bender iso175 |  | OK | Current Sensor Make/Model |  |  |  | BLANK
Setpoint |  |  | 200 | kΩ | OK | Current Sensor Datasheet |  |  |  | BLANK
 |  |  |  |  |  | Trip Current |  |  | A | BLANK
 |  |  |  |  |  | Sensor Output @ Trip Current |  |  | V | BLANK
 |  |  |  |  |  | Accuracy @ Trip Current |  |  | A | BLANK
Shutdown Circuit Schematic |  |  |  |  |  |  |  |  |  | BSPD System Schematic
Shutdown Circuit Schematic Shows |  |  |  |  |  |  |  | BLANK |  | BSPD System Schematic Shows |  | BLANK
Rules References
EV.7.9 |  | GLVMS |  |  |  |  |  | BLANK |  | BSPD Current Sensor input open/short circuit protection |  | BLANK
EV.7.9 |  | TSMS |  |  |  |  |  | BLANK |  | BSPD Brake Position input open/short circuit protection |  | BLANK
EV.7.10 |  | 2 Side Shutdown Buttons |  |  |  |  |  | BLANK |  | Shutdown circuit powerstage |  | BLANK
EV.7.10 |  | 1 Cockpit Shutdown Button |  |  |  |  |  | BLANK |  | Additional Comments | Rules References
T.3.3 |  | Brake Over Travel Switch (BOTS) |  |  |  |  |  | BLANK |  |  | EV.7.7
T.9.4 |  | Inertia Switch |  |  |  |  |  | BLANK
EV.7.3 |  | AMS |  |  |  |  |  | BLANK
EV.7.6 |  | IMD |  |  |  |  |  | BLANK
EV.7.7 |  | BSPD |  |  |  |  |  | BLANK
EV.5.5.2 |  | HVD Interlock |  |  |  |  |  | BLANK |  | TSAL Schematic
EV.7.1.4 |  | IMD, AMS, BSPD have independent power stages |  |  |  |  |  | BLANK
EV.4.1.3 |  | Outboard Wheel Motor Interlocks |  |  |  |  |  | BLANK
 |  | GLV Battery |  |  |  |  |  | BLANK
 |  | HV DC/DC converter GLV connection (if applicable) |  |  |  |  |  | BLANK
T.9.2.2 |  | GLV Fuse |  |  |  |  |  | BLANK
 |  | Wire Gauge |  |  |  |  |  | BLANK
EV.7.1.2 |  | Precharge Contactor coil |  |  |  |  |  | BLANK
EV.7.1.2 |  | Positive AIR coil |  |  |  |  |  | BLANK
EV.7.1.2 |  | Negative AIR coil |  |  |  |  |  | BLANK
EV.5.6.3a |  | Discharge Contactor coil |  |  |  |  |  | BLANK
EV.7.9.1; EV.7.9.3 |  | TSMS is last switch |  |  |  |  |  | BLANK
EV.7.9.1; EV.7.9.2 |  | GLVMS is first switch |  |  |  |  |  | BLANK
 |  | Uses proper electrical schematic symbols |  |  |  |  |  | BLANK
 |  | Labels/text are readable (zooming in is acceptable) |  |  |  |  |  | BLANK
EV.5.10 |  | Interlocks on TS connectors outside of an enclosure |  |  |  |  |  | BLANK
Additional Comments |  |  |  |  |  |  | Rules References
 |  |  |  |  |  |  | EV.7.1 EV.7.2
 |  |  |  |  |  |  |  |  |  | TSAL Schematic Shows |  | BLANK
 |  |  |  |  |  |  |  |  |  | TSAL controlled by >60V present in TS |  | BLANK
 |  |  |  |  |  |  |  |  |  | TSAL powered by GLV |  | BLANK
 |  |  |  |  |  |  |  |  |  | TSAL flashes red when HV present and solid green when not |  | BLANK
 |  |  |  |  |  |  |  |  |  | Additional Comments | Rules References
 |  |  |  |  |  |  |  |  |  |  | EV.5.9

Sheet: Torque Security
Status | BLANK
APPS Sensor Transfer function |  |  |  | BLANK | Torque Control Path Security Checks |  |  |  |  |  |  |  |  | BLANK
Rules Reference |  | T.4.2.3
Position | APPS1 Output [V] |  | APPS2 Output [V] |  | Source Device | Destination Device | Communication | Redundant | Out Of Range | Correlation | Checksum | Timeout | Other |  | Additional Comments
0% |  |  |  | BLANK
20% |  |  |  | BLANK | APPS |  |  |  |  |  |  |  |  | BLANK
40% |  |  |  | BLANK
60% |  |  |  | BLANK
80% |  |  |  | BLANK
100% |  |  |  | BLANK

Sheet: Other
Status | BLANK
Motor Controller |  |  |  | OK | Motor |  |  | OK
Make |  | Rinehart Motion Systems LLC |  | OK | Make |  | Emrax | OK
Model |  | PM100DX |  | OK | Model |  | 228 HV CC | OK
Datasheet |  | PM100DX (https://www.cascadiamotion.com/images/catalog/DataSheets/PM100.pdf) |  | OK | Datasheet |  | Emrax 228 (https://emrax.com/wp-content/uploads/2017/01/emrax_228_technical_data_4.5.pdf) | OK
Galvanic Isolation between TS and control |  | 1000 | V | OK
Picture of Energy Meter download connector on car to prove compliance with EV.3.2.2
Energy Meter Download Picture Shows |  |  |  |  |  | BLANK
Energy Meter Download Connector |  |  |  |  |  | BLANK
Additional Comments

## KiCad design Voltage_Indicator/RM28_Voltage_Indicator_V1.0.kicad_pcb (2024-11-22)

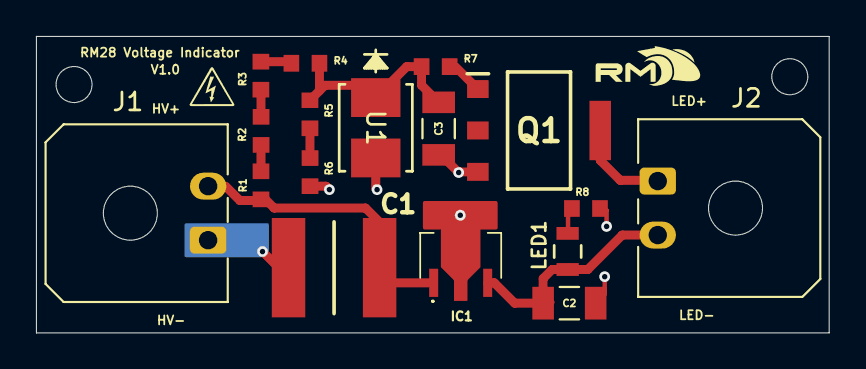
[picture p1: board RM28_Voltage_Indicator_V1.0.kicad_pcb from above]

Board: 2 copper layers, 44.0 x 16.5 mm, 17 parts (0 on the bottom side), 11 nets.

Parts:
C1: 2.2μf; CAPC6153X670N
C2, C3: 22μf; CAPC3216X180N
IC1: NCP785AH120T1G; MC78L05ACHX_1
J1, J2: Molex_Micro-Fit_3.0_43650-0200_1x02_P3.00mm_Horiz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; Molex_Micro-Fit_3.0_43650-0200_1x02_P3.00mm_Horizontal
LED1: CMD17-21VRD/TR8; LED0805N_CML
Q1: SBCP56-16T1G; SOT230P700X175-4N
R1, R2, R3, R4: 240kΩ; RESC1608X55N
R5: 20kΩ; RESC1608X55N
R6, R8: 1kΩ; RESC1608X55N
R7: 10kΩ; RESC1608X55N
U1: 1SMB5927BT3G; SMB_ONS

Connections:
/+HV: C1.1, IC1.1 (VIN), J1.2, R1.1
GND: C1.2, C2.2, C3.2, IC1.2 (GND_1), IC1.4 (GND_2), J1.1, Q1.3 (E), R6.2, R8.2, U1.2 (ANODE)
unnamed: C2.1, IC1.3 (VOUT), J2.2, LED1.1
unnamed: LED1.2, R8.1
unnamed: Q1.1 (B), R7.2
unnamed: J2.1, Q1.4 (C_2)
unnamed: R1.2, R2.1
unnamed: R2.2, R3.1
unnamed: R3.2, R4.1
unnamed: R5.2, R6.1
unnamed: C3.1, R4.2, R5.1, R7.1, U1.1 (CATHODE)

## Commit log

2024-09-27 Accumulator Indicator Schematic
    [RM28 Accumulator Indicator.kicad_sch]
2024-09-27 RM28 Accumulator Indicator Layout
    [RM28 Accumulator Indicator.kicad_pcb]
2024-10-04 RM28 ESF V1.0 Draft
    [ESF Copy V1.0.xlsx]
2024-10-08 change rail voltages throughout to match shutoff circuit logic
2024-10-11 RM28 Voltage indicator w/ trace fixes
    [RM28 Voltage Indicator.kicad_pcb]
2024-10-18 Silkscreen changes, GLV side
    [RM28 RTML.kicad_pcb]
2024-10-18 Fixed silkscreen on HV Side
    [RM28 RTML.kicad_pcb]
2024-10-18 flip comparator circuit to standard orientation in BSPD
2024-10-18 limiting current draw by using realistic sensing resistances
2024-10-30 started implementing more changes for proper BSPD with current shutdown circuit design
    [BSPD Current Sensor Trip Calculator.xlsx]
2024-10-30 BSPD circuit topolgy fixed, logic is very close to working
2024-10-30 BSPD logic works! Need to tune to perfect window to be within rules, also need to switch to 5V logic with 12V output
2024-10-30 BSPD is in testable state, does not hold 12V once triggered, and does not use real world reference voltages yet
2024-10-30 created latching relay, switch just needs to be modeled for simulation
2024-11-01 Updated RTML silkscreen
    Silkscreen now shows >4mm spacing
    [RM28 RTML.kicad_pcb]
2024-11-01 RM28 Tractive System Schematic V1.0
    [ESF.kicad_sch]
2024-11-01 BSPD is fully functioning, many changes. Cannot simulate latching relay circuit
2024-11-08 Complete RM28 ESF V1.0
    [RM28_ESF_V1.0.xlsx]
2024-11-08 RM28 Voltage Indicator V1.0
    [RMS HV Indicator.kicad_pcb]
2024-11-08 reformated directory of this repo, easier to find individual project
    [BSPD Current Sensor Trip Calculator.xlsx, ESF Copy V1.0.xlsx, ESF.kicad_sch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]
2024-11-15 Silkscreen edits
2024-11-19 Layout updates
    [RM28_Voltage_Indicator_V1.0.kicad_pcb]
2024-11-19 Final changes for layout
    [RM28_Voltage_Indicator_V1.0.kicad_pcb]
2024-11-19 Added gerbers
2024-11-19 Update README.md with current existing circuits
2024-11-19 reorganization of misc files, more deleting more old files, matching file structure of readme
    [RM28 Accumulator Indicator.kicad_pcb, RM28 Accumulator Indicator.kicad_sch, RM28 RTML.kicad_pcb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]
2024-11-22 Final layout changes
    [RM28_Voltage_Indicator_V1.0.kicad_pcb]
2024-12-05 Test draft of RM27 FW
    Changed faults for battery health and thermistor disconnections
